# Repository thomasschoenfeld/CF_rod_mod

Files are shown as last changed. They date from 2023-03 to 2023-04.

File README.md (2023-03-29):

# CF ROD MOD
a carbon fiber mod with rods instead of a square x-beam and without the linear rails
- extruder > Hextrudort
- hotend > Goliath
- no other combinations are currently supported, but the fusion file is available so knock yourself out :-)

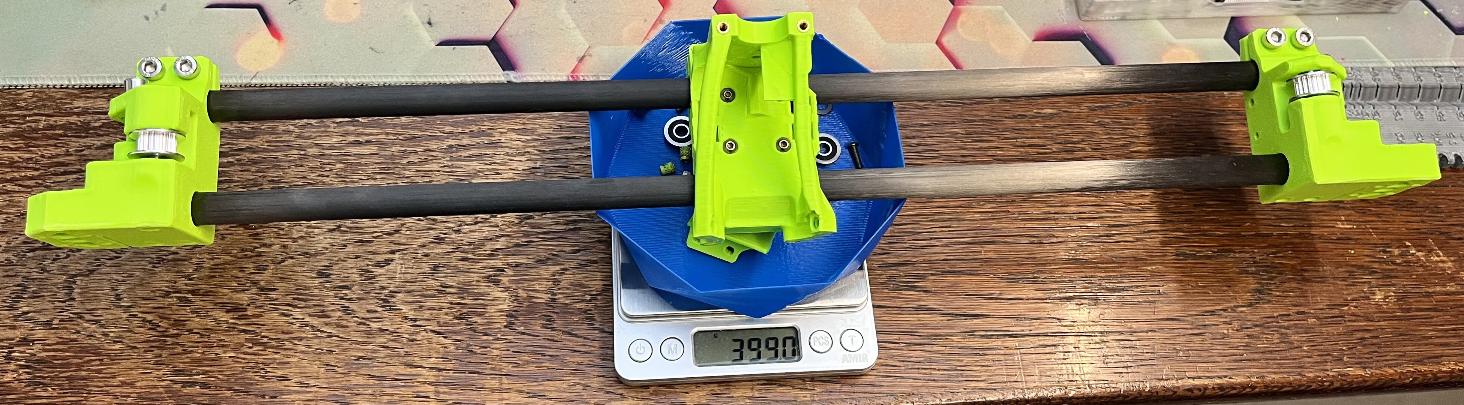
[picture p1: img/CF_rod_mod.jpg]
cf mod


THIS MOD IS STILL ALPHA!

This mod is designed to essentially reduce the weight on the x axis of the gantry of a Voron 2.4 by about half. It uses 12mm carbon fiber rods and IGUS bushings. As this mod is still ALPHA. 

current version v3 - changelog
- the carriage has been completely redesigned. It is now printed on its side, thereby allowing very tight tolerances. it also allows to print easily modify the spacing between the bushings as well as the diameter of the cut-out. This way one can simply print a couple of them in various sizes and use the one that fits best. This is all in all a big step into the right direction, because now the normal IGUS RJ4J bushings can be ordered and used, even if the CF rods are not up to specs. One simply uses the pressure of the carriage on the IGUS bushings, to tighten thing so the desired fit. This also means, the bushings do not need to be secured anymore, as they simply hold with the pressure of the carriage, while still gliding smoothing on the CF rod. However the sides of the toolhead are designed in way, that would still hold the bushing, should they slip out.
- the sketch to easily modify the spacings is included
- accordingly the toolhead had to modified to accommodate the new carriage, which included strengthening of some parts on the toolhead. No other functional changes have been made. 
- currently only supports Beacon3D. If you ready this, just buy 2 or 3. They are well with the money. I will add klicky support, if this version is successful enough  and holds up to my expectations. 

older versions... moved to a subfolder, just FYI and no further developemnt on those:
- compact > rod closer together and the AB joints therefore shorter
- hightower > rods further apart, improving vertical stability, but may have issues with binding of the IGUS as well as torque on the AB joints
- hightower dual rail > using MGN9 rails on the top and bottom of the Y axis, improving stability but also increasing the weight.

Log 2023-03-27 // FYI
After printing an testing the first version, following things came to light:
- B motor was loose… great stuff… all my measurements in the last 2 weeks are worthless. 
- the main issue however are tolerances. Buying an expensive CF rod from IGUS together with the Rj4J, which certainly is an option, would cost more than 100€, which all things considered, is still okay. Cheap CF from eBay or AliExpress will typically be not up to specs. One way I tried solving this, by allowing the bushings to be squished, changed the geometry and orientation etc… but nothing really worked well…. 
- I found out, that IGUS also sells the base material of its bushing as a normal 3D printable filament. This for one solves the tolerance issues and while not cheap, about 70€ for a 750g spool, you can simply measure and test-print you own bushings. Once you have perfectly smooth bushing on the given CF rod, you can adjust the toolhead tolerances accordingly.
- Since I am now aware of the IGUS filament, a bunch of new ideas come to mind. For example a aluminium square tube 22x20mm, which is about 175g for a 430mm long tube, could be used as rail and a custom bushing around it. More to come on this idea.
- the toolhead can now only be swapped by taking out the whole x-axis. This is a trade off, better stability but a bit more work
END LOG

fully assmebled with the toolhead-carriage module >> 399g (minus 18.1g for missing titianium screws >> 380,9g)

fully alu x
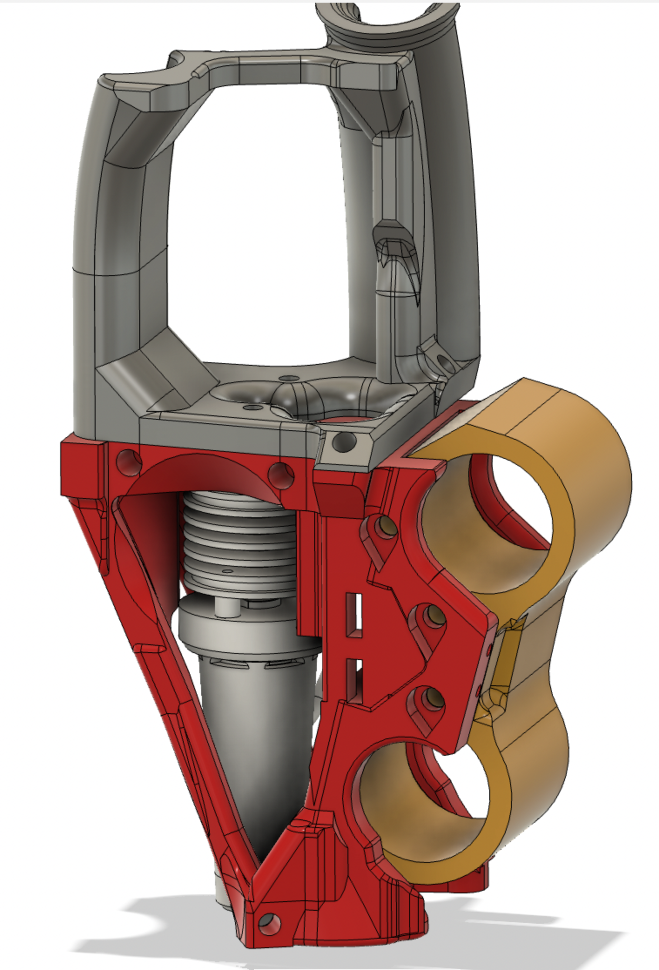
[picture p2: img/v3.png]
v3

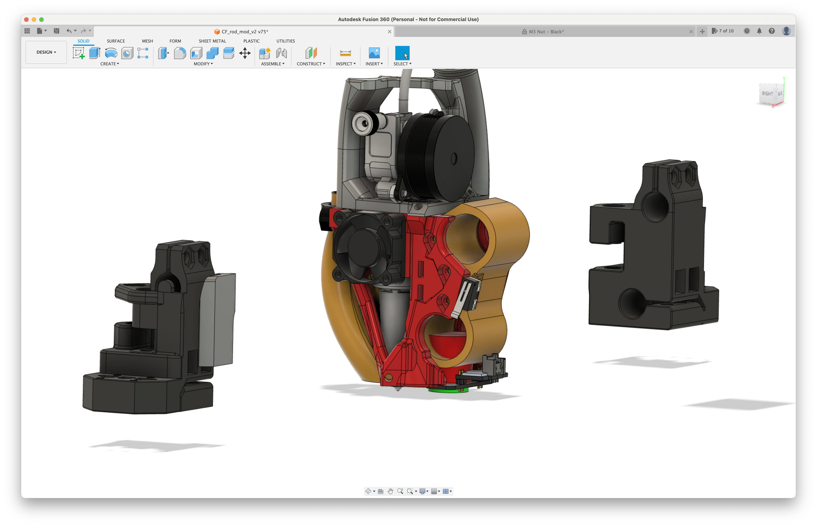
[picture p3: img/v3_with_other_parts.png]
v3 with other parts


The ultra light weight full aluminium X (Fystec ultra light aluminium X beam and light weight aluminium CNC'ed AB joints) with all titianum screws ends up at 490.2g.
The Carbon Fiber ROD MOD comes in at 380,9g* (399g but I was missing some titanium screws / nuts).

490,2g - 380,9g = 109,3g or 77.7% > 22.3% lighter

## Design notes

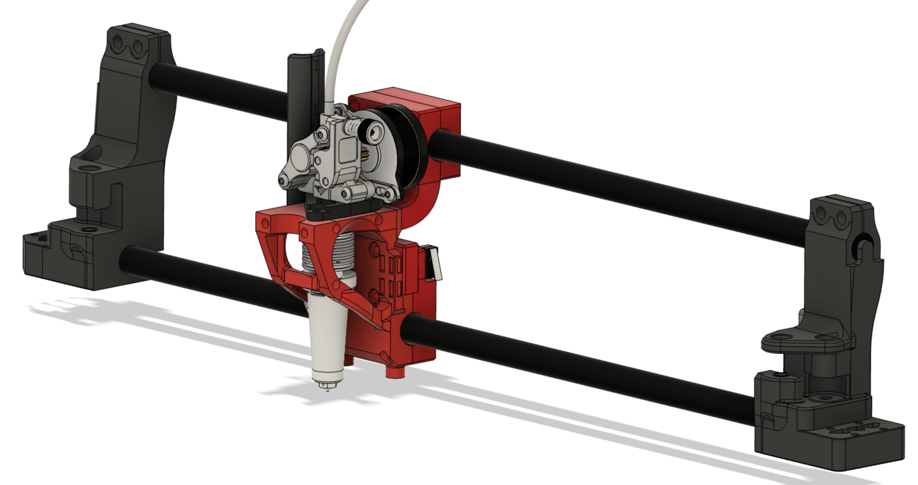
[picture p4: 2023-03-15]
img/hightower.png

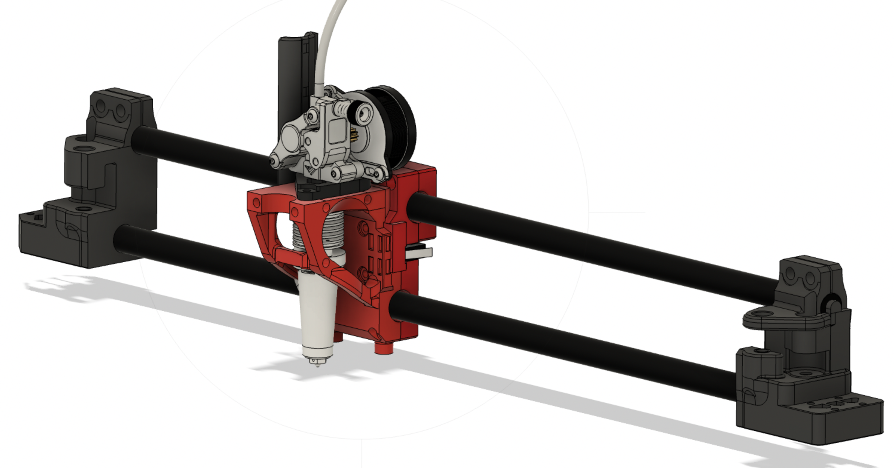
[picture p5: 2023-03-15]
img/compact.png

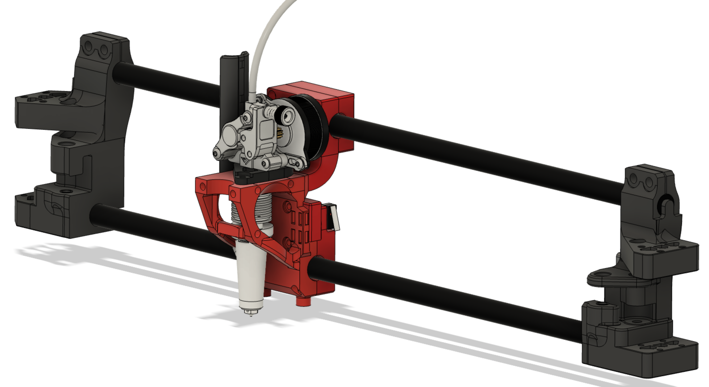
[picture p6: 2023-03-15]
img/hightower_dual_rail.png

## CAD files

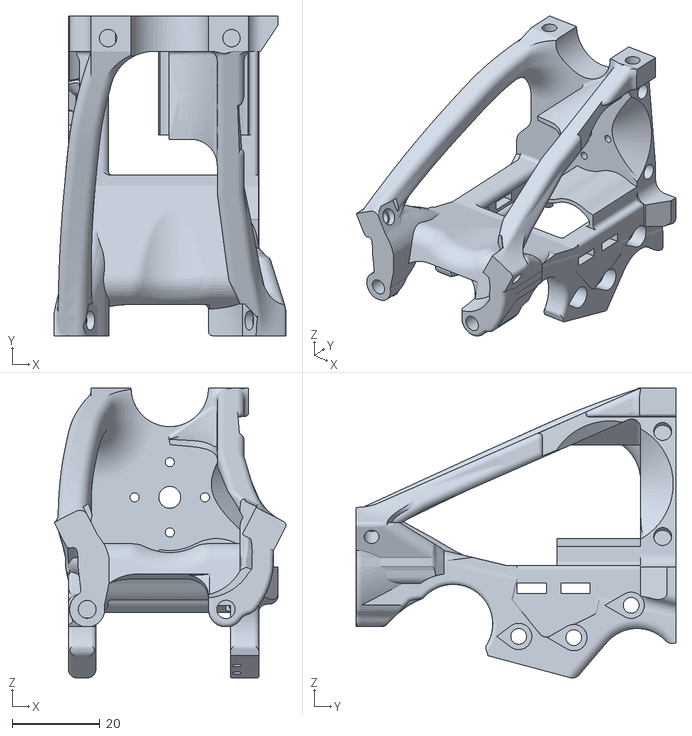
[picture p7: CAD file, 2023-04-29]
v3/CF_ToolHhead_v3.stl
52.8 x 72.8 x 66.0

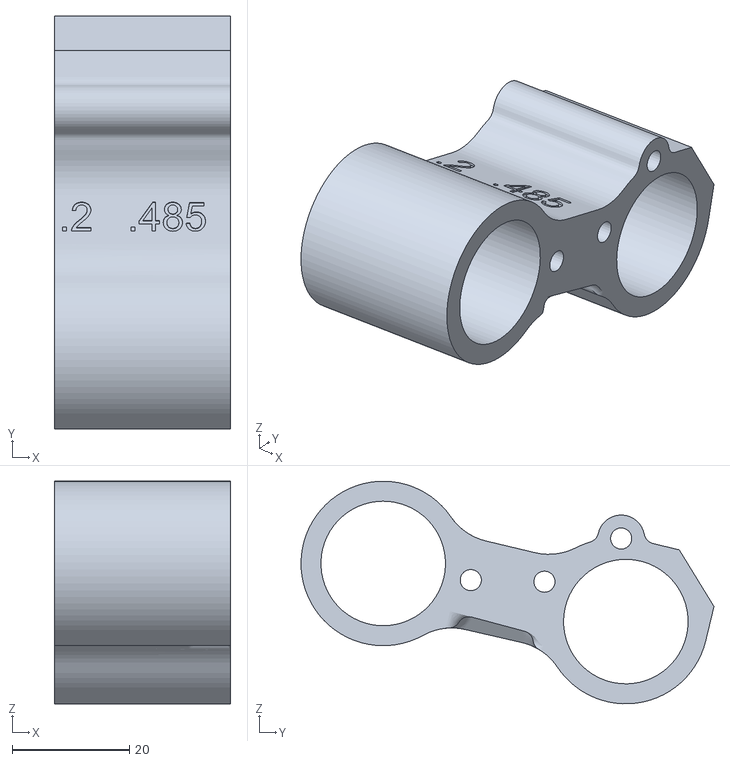
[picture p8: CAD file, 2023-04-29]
v3/MyCarriage_21.2_42.485.stl
30.0 x 70.3 x 37.9

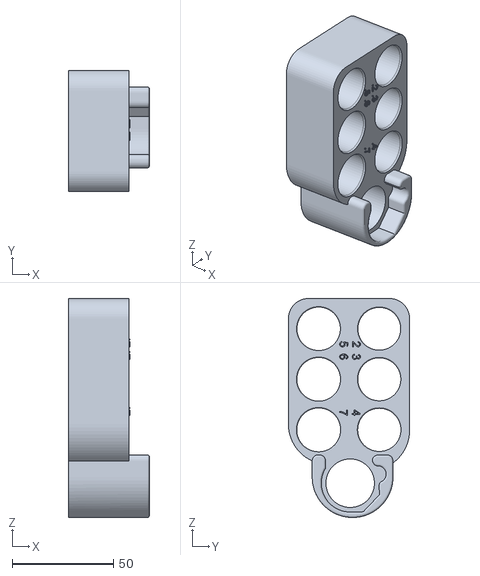
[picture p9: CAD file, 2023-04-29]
v3/IGUS-tester_v3.stl
40.0 x 60.0 x 108.4

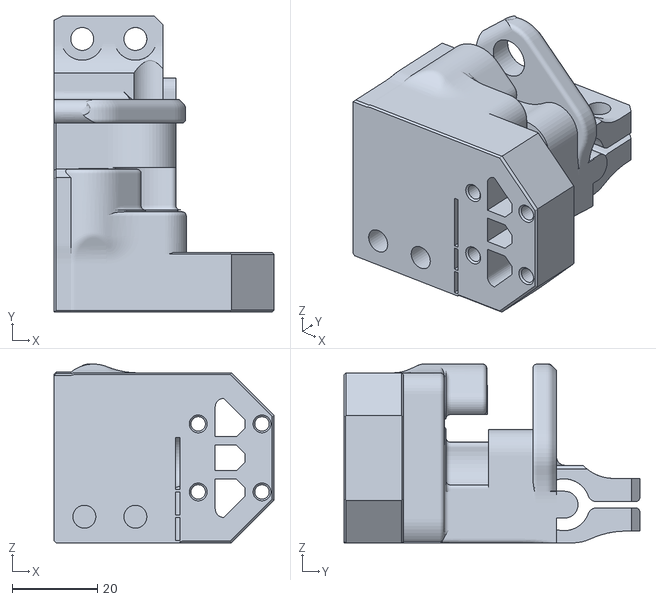
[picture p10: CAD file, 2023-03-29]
v3/xy_joint_right_v1.3.stl
51.7 x 69.6 x 42.1

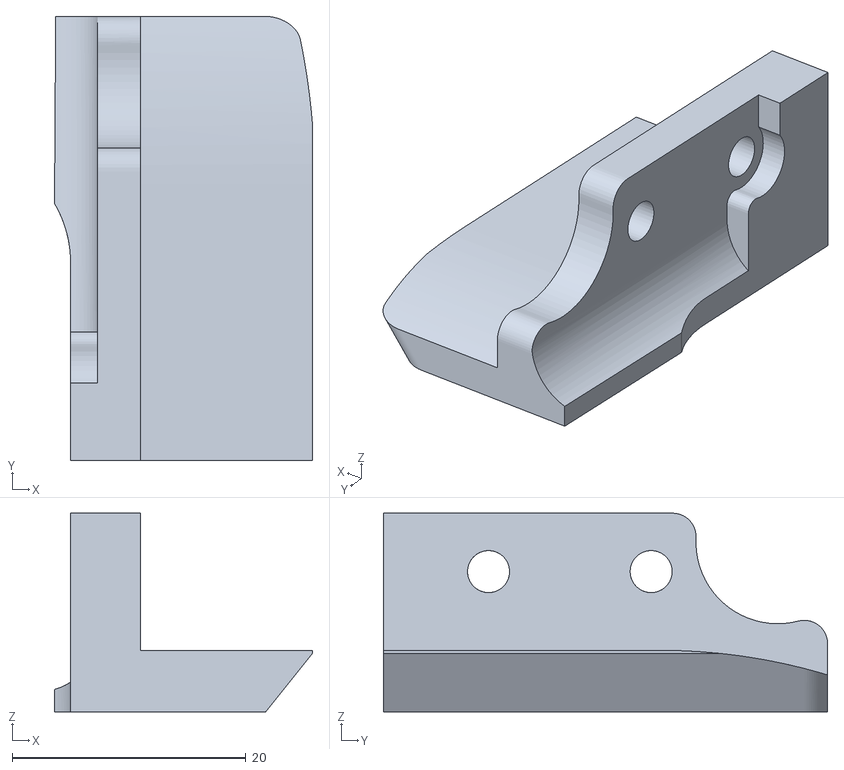
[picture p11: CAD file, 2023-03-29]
v3/Endstop-spacer_CF.stl
22.1 x 38.0 x 17.0

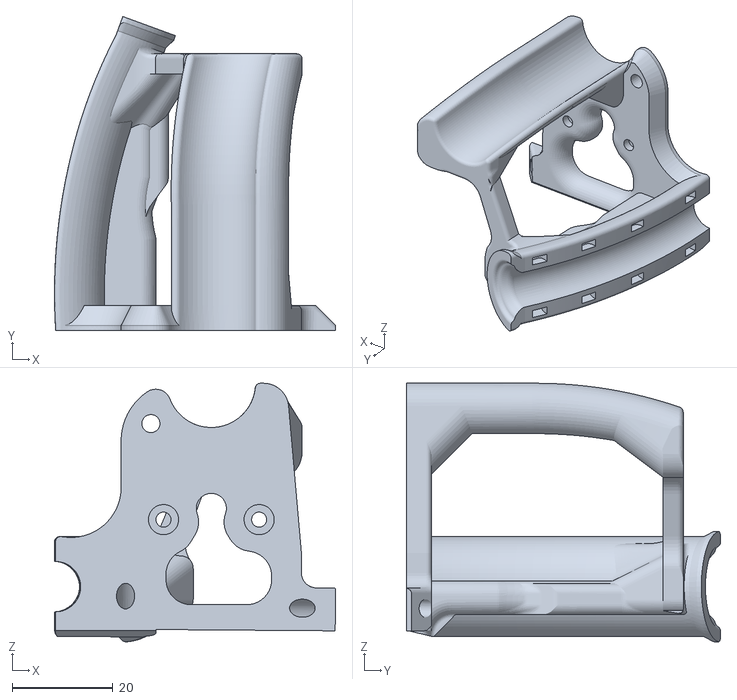
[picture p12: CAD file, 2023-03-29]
v3/Hex_adapter_w_cage.stl
55.9 x 62.4 x 51.4

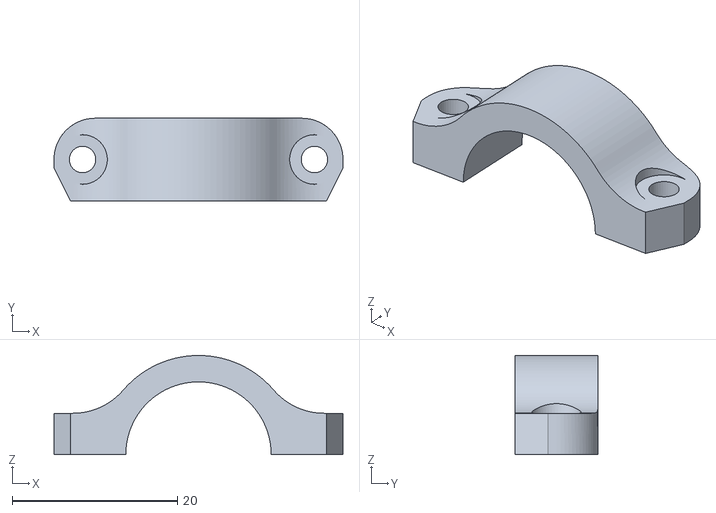
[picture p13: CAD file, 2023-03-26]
v3/Clamp_3.0.stl
35.0 x 10.0 x 12.0

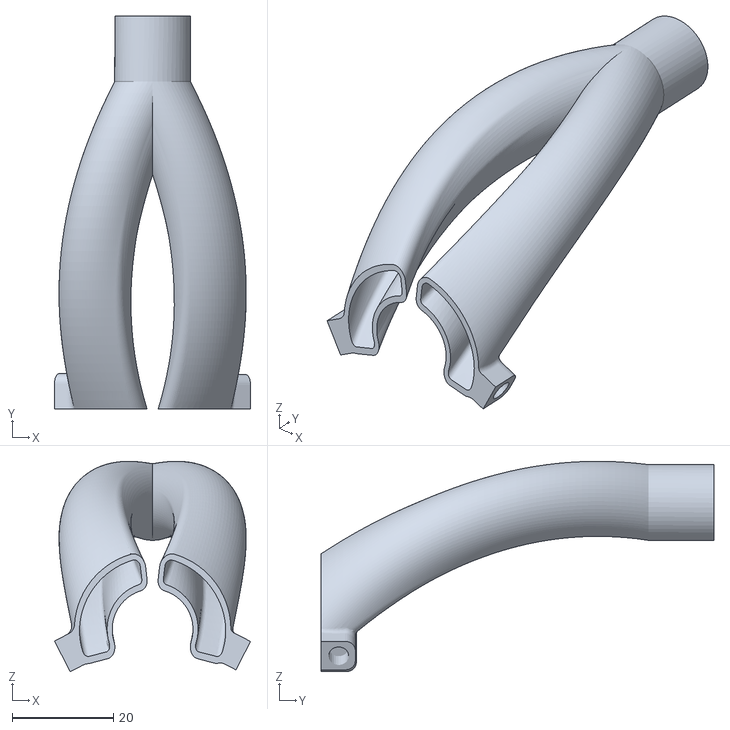
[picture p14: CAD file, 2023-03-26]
v3/Duct_v6.3.stl
38.8 x 77.8 x 41.6

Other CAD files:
v3/MyCarriage_21.2_42.4.stl
v3/MyCarriage_21.22_42.485.stl
v3/MyCarriage_21.2_42.3.stl
v3/MyCarriage_21.28_42.485.stl
v3/MyCarriage_21.14_42.485.stl
v3/MyCarriage_21.26_42.485.stl
v3/MyCarriage_21.18_42.485.stl
v3/MyCarriage_21.24_42.485.stl
v3/MyCarriage_21.16_42.485.stl
v3/xy_joint_left_v1.3.stl
older_versions/compact/CF_ToolHhead_v2.4.stl
older_versions/compact/CF_ToolHhead_v2.4_plus0.1.stl
older_versions/compact/CF_ToolHhead_v2.5_plus0.2.stl
older_versions/compact/Endstop-spacer_CF.stl
older_versions/compact/Hex_adapter_w_cage.stl
older_versions/compact/IGUS_stopper_bottom.stl
older_versions/compact/IGUS_stopper_bottom_2.2.stl
older_versions/compact/IGUS_stopper_top.stl
older_versions/compact/IGUS_stopper_top_2.1.stl
older_versions/compact/xy_joint_left_v1.3.stl
older_versions/compact/xy_joint_right_v1.3.stl
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

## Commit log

2023-03-15 initial upload
    [CF_mod_v2_Voron2.4 CF rod MOD v1_CF_toolhead_goliath.stl, CF_mod_v2_Voron2.4 CF rod MOD v1_Endstop-space.stl, CF_mod_v2_Voron2.4 CF rod MOD v1_HEx-adapter_v2_C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]
2023-03-16 step file upload
    [CF_mod_v3_Voron2.4 CF rod MOD v1_CF_mod_Toolhead_v3.stl, CF_mod_v3_Voron2.4 CF rod MOD v1_Endstop-space.stl, CF_mod_v3_Voron2.4 CF rod MOD v1_HEx-adapter_v2_CF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]
2023-03-16 parts as single files
    [CF_rod_lower.step, CF_rod_upper.step, Carriage_p1.step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]
2023-03-21 updated toolhead and extruder plate
    [CF_mod_Toolhead_v3.1.stl, HEx-adapter_v3.stl]
2023-03-22 minor fixed and first build pictures
    [CF_mod_v3_Voron2.4 CF rod MOD v1_CF_mod_Toolhead_v3.stl, CF_mod_v3_Voron2.4 CF rod MOD v1_HEx-adapter_v2_CF_MOD.stl, CF_mod_v3_Voron2.4 CF rod MOD v1_Rod_carri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]
2023-03-22 fix to allow more IGUS squish
    [CF_mod_Toolhead_v3.1.stl, CF_mod_Toolhead_v3.3.stl, CF_mod_v3_Voron2.4 CF rod MOD v1_Rod_carriage_v2_p4.stl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]
2023-03-26 updated v2
    [CF_ToolHhead_v4.stl, CF_mod_Toolhead_v3.3.stl, CF_mod_v3_Voron2.4 CF rod MOD v1_Endstop-space.stl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]
2023-03-26 updated toolhead
    [CF_ToolHhead_v2.stl, CF_ToolHhead_v4.stl]
2023-03-26 improved geometry
    [CF_ToolHhead_v2.1.stl, CF_ToolHhead_v2.stl, IGUS_Top_clamp.stl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]
2023-03-28 smaller updates for tolerances
    [CF_ToolHhead_v2.4_plus0.1.stl, CF_ToolHhead_v2.5_plus0.2.stl, IGUS_stopper_bottom_2.2.stl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]
2023-03-29 new version 3
    [CF_ToolHhead_v2.4.stl, CF_ToolHhead_v2.4_plus0.1.stl, CF_ToolHhead_v2.5_plus0.2.stl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]
2023-04-29 update toolhead and testers
    [CF_ToolHhead_v3.stl, IGUS-tester_v3.stl, MyCarriage_21.14_42.485.stl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]
